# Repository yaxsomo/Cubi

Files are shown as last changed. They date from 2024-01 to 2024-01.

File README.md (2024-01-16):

### Description
Simple open source bluetooth controlled wheeled robot. Mechanical design, electronics and software designs available on this repo.
I used @Gregwar's Holo as a starting point.

The initial design is a cube like robot :

https://www.youtube.com/watch?v=2ZDV0_4vD0g

https://www.youtube.com/watch?v=TOusHRbKWQg

A second design was also made to play around cart-poling:

https://www.youtube.com/watch?v=Ubej95gH9Gs

TODO:

- Add Julien's O. designs and events

- Add Julien's A. and Jérémy's designs and event (cap science)

### Simulation
Some simulation stuff (simple kinematic control, inverted pendulum tests) is available in Python here :
https://bitbucket.org/RemiFabre/cubi/src/master/simulation/

0) Installation
You'll need Python (any version should work) and pygame
```
pip install pygame
```

1) Simple control of a wheeled robot (click around)
```
python main.py
```
https://www.youtube.com/watch?v=O8ZoUAvGYmE

2) Inverted pendulum (cart-pole) simulation
```
python cart_pole.py
```
https://www.youtube.com/watch?v=xhEcLnnj7fg

### How to make it work
You'll have to install the arm cross-compilation tools. On debian-like distributions,
you can get it with:

```
    sudo aptitude install build-essential git-core dfu-util openocd python \
        python-serial binutils-arm-none-eabi gcc-arm-none-eabi libstdc++-arm-none-eabi-newlib
```
If you're running an Ubuntu 14.04 or older, you might need to install the libstdc++-arm-none-eabi-newlib packet by hand. Download link :
http://ftp.de.debian.org/debian/pool/main/libs/libstdc++-arm-none-eabi/libstdc++-arm-none-eabi-newlib_4.8.3-9+4_all.deb

Command (if a conflict rises, you can add --force-overwrite to the following line):
```
	sudo dpkg -i libstdc++-arm-none-eabi-newlib_4.8.3-9+4_all.deb
```

Then go to Cubi/firmware/src and run :

```
bash ./prepare.sh
```

Then, go to the `firmware/` directory and edit the `Makefile` to set the appropriate
`BOARD` variable, targetting your servo.

You can then run:

```
make
```

Use an USB cable to connect your pc with the robot's board

```
make install
```
If you didn't follow this section to setup udev rules, you might need to ```sudo make install``` instead

http://static.leaflabs.com/pub/leaflabs/maple-docs/0.0.12/unix-toolchain.html#toolchain-udev

### Bluetooth
You can control the robot without the need of a cable. The most straight-forward way is to download the "Metabot" app from Google Play. Once on the app you can scan for devices, find your robot and pair it with your phone.

If you want to pair your PC with your robot, one method is as follows (Ubuntu).

Uninstall modemmanager (not needed but causes some issues)

```
    sudo apt-get purge modemmanager
```

Scan for bluetooth devices and save the adress (e.g. 98:D3:37:90:ED:D6) of your robot. For example, we use blueman-manager :

```
    sudo apt-get install blueman
    sudo blueman-manager
```

Assign a serial port to the connection. You can do that on the graphical interface of blueman-manager but doing it directly with rfcomm seems more robust :

```
    sudo rfcomm bind /dev/rfcomm0 98:D3:37:90:ED:D6
```

Now you can access the remote terminal on the robot with :

```
    cu -l /dev/rfcomm0
```

You might have permission access issues. Make sure you're in the dialout group or go bonkers :

```
    sudo chmod 777 /dev/rfcomm0 && cu -l /dev/rfcomm0
```

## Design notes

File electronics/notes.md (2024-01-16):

Pour exporter la board depuis Eagle pour la tirer (Fonctionne sous Eagle 8) :
File->CAM Processor -> Load Job File -> /eagle/sfe-gerb274x.cam  (fichier from Sparkfun)
Gerber RS-274X

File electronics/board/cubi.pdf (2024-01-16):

Pré-placement

On limite les boucles de courant fort. Dans ce cas, ca va être chiant, le connecteur du moteur étant juste complètement débile, la puissance passant sur les broches externe.
On peut quand même remarquer que M1 est gardé par une masse et M2 par VCC. On ajoute donc une capa de découplage entre Vcc et la masse, qui devra être placé au cul du connecteur.

On limite ainsi la casse : en HF, les fils de puissance M1 et M2 sont « blindé » par la masse.

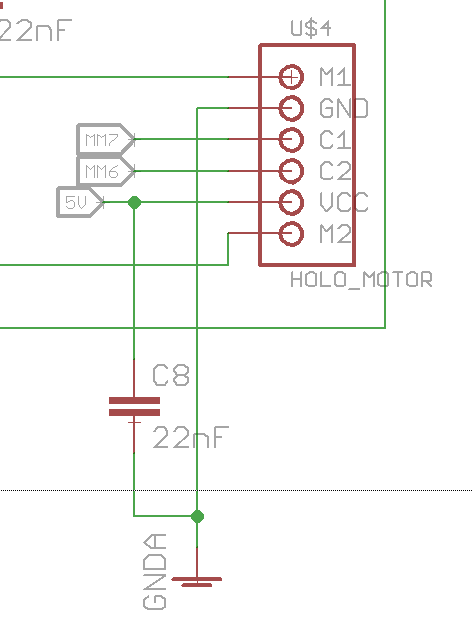
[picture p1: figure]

On place donc les connecteurs au plus court du pont. On limite ainsi les zones dangereuses (en jaune sur la figure). Dans ces zones, on fera particulièrement attention à ne pas fendre le plan de masse. Aucune piste sensible de doit traverser ces zones.

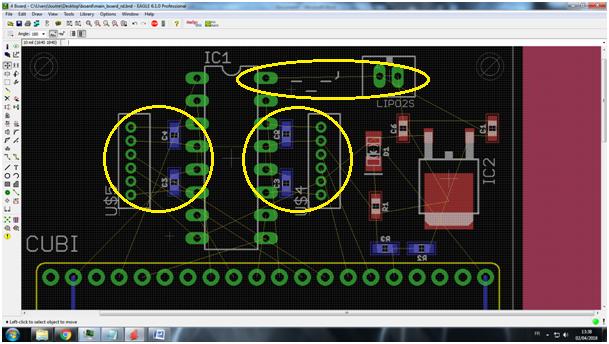
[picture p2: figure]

On tire les pistes fort courant en premier, pour voir à quoi on doit s’attendre. On passe ensuite quelques pistes de commande, pour avoir une idée du routage. On peut essayer de passer une alim au deux.

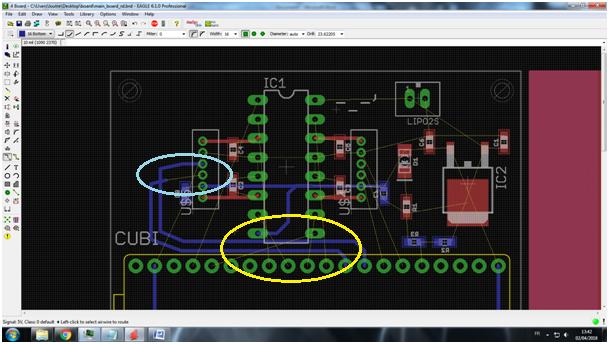
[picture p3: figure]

Premier constat : en bleu, les sorties codeurs croisent. Plus grave en jaune, là on sens que ca va être Beyrouth. Après étude du schéma, on voie que les fils non routé sont les PWM, donc des signaux rapide. Tant pis pour l’alim, elle dégage, on privilégie les signaux rapide au routage. On en profite pour réafecter les E/S pour que cela ne croise pas.

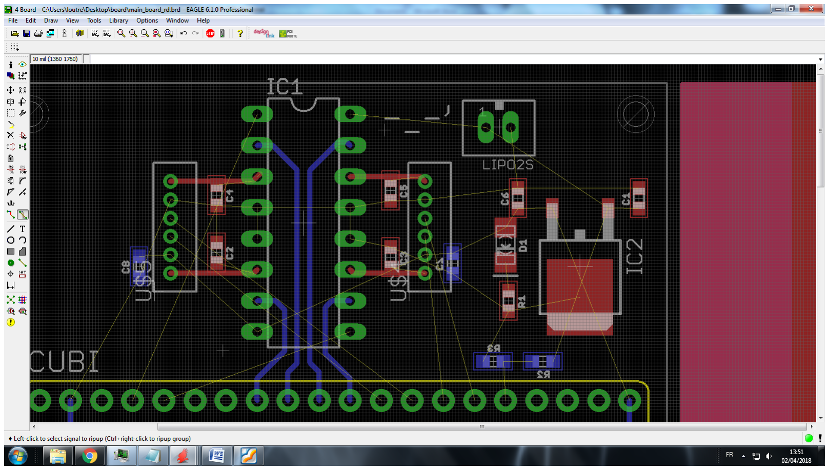
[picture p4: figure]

On passe toutes les PWM en BOTTOM : comme cela, le plan de masse en top fera écran (passer des pistes sous un composant de puissance, c’est dangereux, le composant rayonne, ce qui peut pourris les signaux)

On reprend le routage des codeurs :

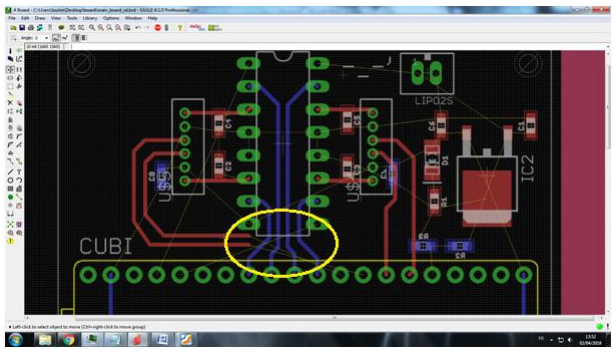
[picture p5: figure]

En jaune, c’est la seconde guerre du Golf. On doit croiser les codeurs avec les PWM, donc fendre le plan de masse. Or, pour rappel, règle N°1 en routage : ON NE FEND JAMAIS UN PLAN DE MASSE (Bordel). Bon, là on est en deux couches donc, on se détend.
Règle N°2 du routage : en deux couches, si on doit croiser des pistes, on se réfère à la règle N°1.

Dans notre cas, on fait le tour par le haut.

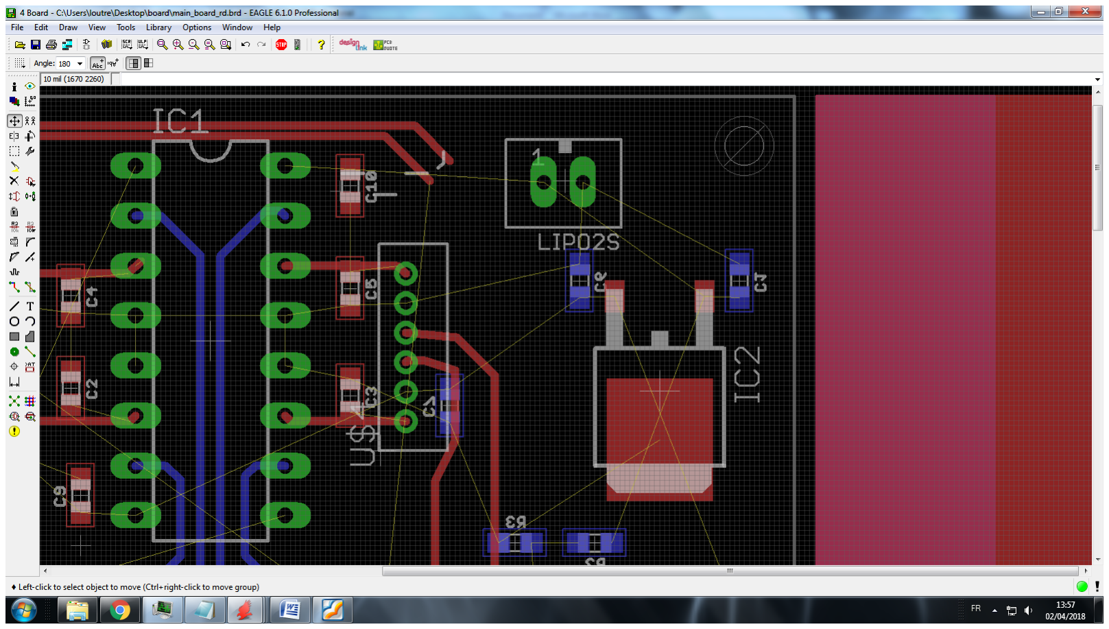
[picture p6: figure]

Bon c’est pas top. Mais a défaut… on va croiser l’alim mais avec les capas de découplages ca devrait aller (Les capas sur VCC1 et VCC2 ont été ajouté, elles avaient été oublié)

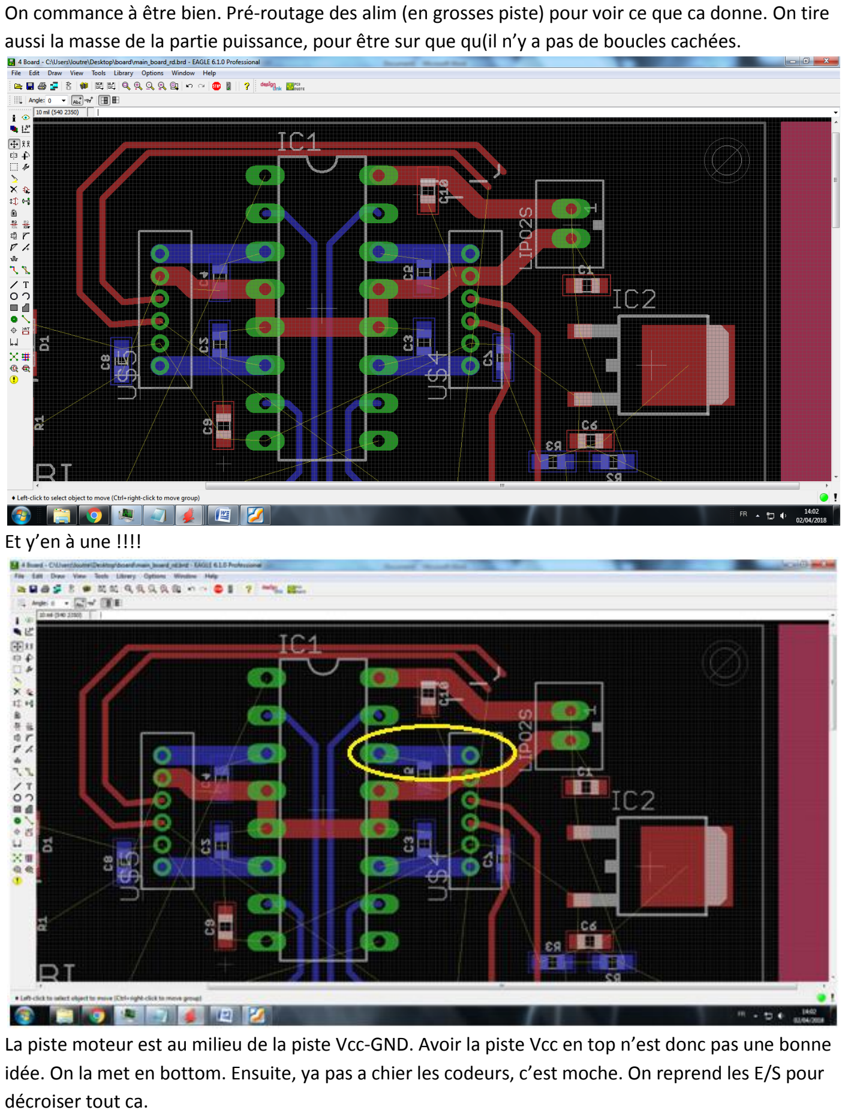
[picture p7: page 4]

On commance à être bien. Pré-routage des alim (en grosses piste) pour voir ce que ca donne. On tire aussi la masse de la partie puissance, pour être sur que qu(il n’y a pas de boucles cachées.

Et y’en à une !!!!

La piste moteur est au milieu de la piste Vcc-GND. Avoir la piste Vcc en top n’est donc pas une bonne idée. On la met en bottom. Ensuite, ya pas a chier les codeurs, c’est moche. On reprend les E/S pour décroiser tout ca.

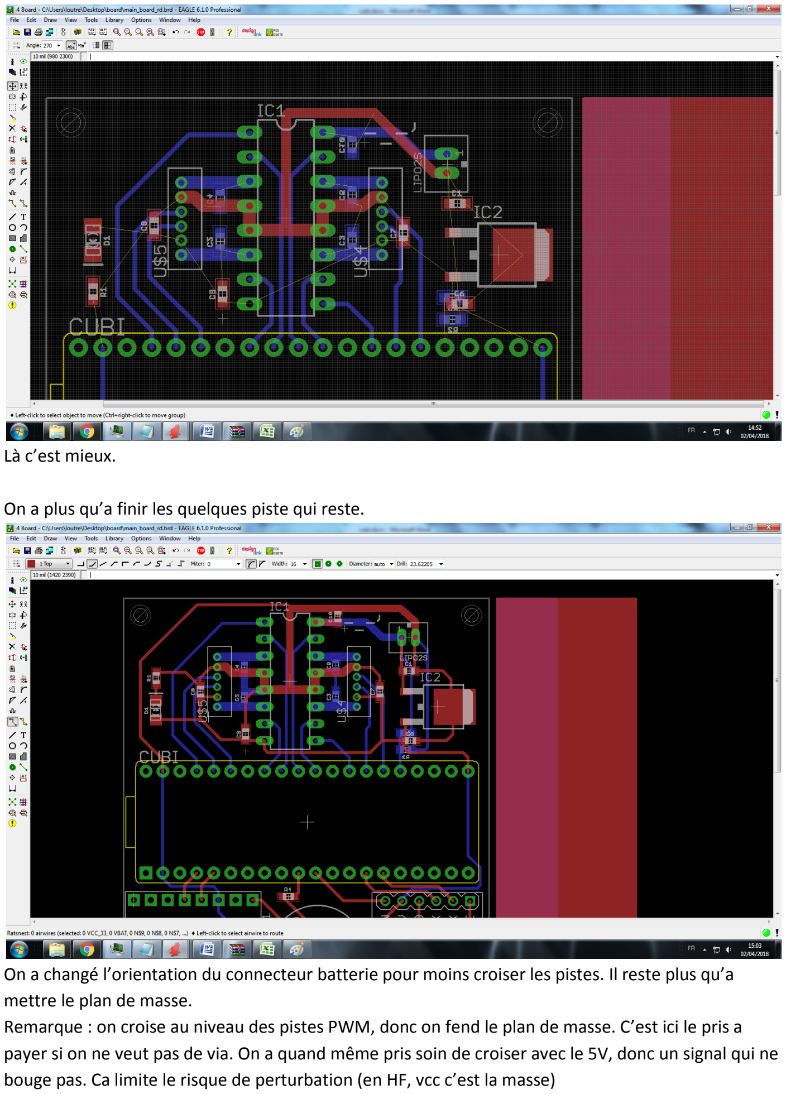
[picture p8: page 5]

Là c’est mieux.

On a plus qu’a finir les quelques piste qui reste.

On a changé l’orientation du connecteur batterie pour moins croiser les pistes. Il reste plus qu’a mettre le plan de masse.
Remarque : on croise au niveau des pistes PWM, donc on fend le plan de masse. C’est ici le pris a payer si on ne veut pas de via. On a quand même pris soin de croiser avec le 5V, donc un signal qui ne bouge pas. Ca limite le risque de perturbation (en HF, vcc c’est la masse)

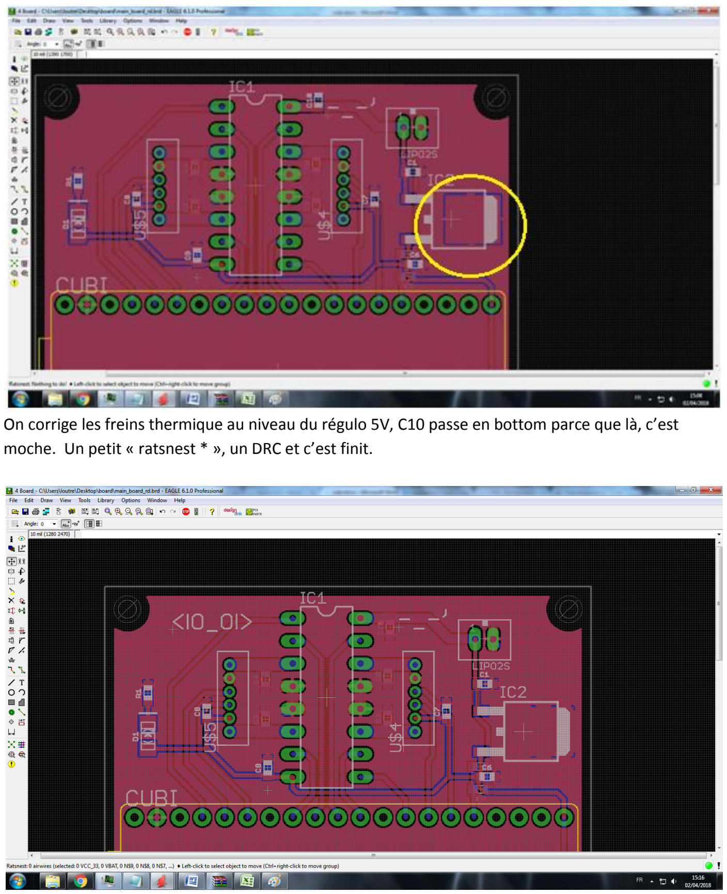
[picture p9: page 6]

On corrige les freins thermique au niveau du régulo 5V, C10 passe en bottom parce que là, c’est moche. Un petit « ratsnest * », un DRC et c’est finit.

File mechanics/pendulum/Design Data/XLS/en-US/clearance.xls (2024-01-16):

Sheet: Ansi Unified Screw Threads
I | Sort Order -1
Fastener Type | Size | Shaft Diameters |  |  | Head Dimensions
 |  | Close | Normal | Loose | Diameter | Depth/Angle | Head Type
Flat Head Machine Screw (82) | #0 | 0.0635 | 0.07 | 0.073 | 0.119 | 82 | 2
Flat Head Machine Screw (82) | #1 | 0.076 | 0.081 | 0.089 | 0.146 | 82 | 2
Flat Head Machine Screw (82) | #2 | 0.089 | 0.096 | 0.1065 | 0.172 | 82 | 2
Flat Head Machine Screw (82) | #3 | 0.104 | 0.11 | 0.12 | 0.199 | 82 | 2
Flat Head Machine Screw (82) | #4 | 0.116 | 0.1285 | 0.136 | 0.225 | 82 | 2
Flat Head Machine Screw (82) | #5 | 0.1285 | 0.136 | 0.154 | 0.252 | 82 | 2
Flat Head Machine Screw (82) | #6 | 0.144 | 0.1495 | 0.1695 | 0.279 | 82 | 2
Flat Head Machine Screw (82) | #8 | 0.1695 | 0.177 | 0.1935 | 0.332 | 82 | 2
Flat Head Machine Screw (82) | #10 | 0.196 | 0.201 | 0.221 | 0.385 | 82 | 2
Flat Head Machine Screw (82) | #12 | 0.221 | 0.228 | 0.246 | 0.438 | 82 | 2
Flat Head Machine Screw (82) | 1/4 | 0.257 | 0.266 | 0.2812 | 0.507 | 82 | 2
Flat Head Machine Screw (82) | 5/16 | 0.323 | 0.332 | 0.3437 | 0.635 | 82 | 2
Flat Head Machine Screw (82) | 3/8 | 0.386 | 0.397 | 0.4062 | 0.762 | 82 | 2
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

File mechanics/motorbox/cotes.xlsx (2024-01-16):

epaisseur | 5 | mm | épaisseur du bois
ecartement | 20 | mm | ecartement entre les deux moteurs
dvis | 3 | mm | diametre vis
largeur | 32 | mm | largeur de la boite moteur
L_fente | 30 | mm | longeur des fentes latéral
L_attache_carte | 15 | mm | longueur du bord pour fixer la plaque de la carte elec
marge_attache_carte | 5 | mm | marge entre la plaque carte et la plaque moteur

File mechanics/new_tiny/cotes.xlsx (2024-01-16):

epaisseur | 6 | mm | épaisseur du bois
ecartement | 25 | mm | ecartement entre les deux moteurs
dvis | 3 | mm | diametre vis
largeur | 32 | mm | largeur de la boite moteur
L_fente | 30 | mm | longeur des fentes latéral
L_attache_carte | 15 | mm | longueur du bord pour fixer la plaque de la carte elec
marge_attache_carte | 5 | mm | marge entre la plaque carte et la plaque moteur
L_cubi | 81.6 | mm | longeur de la boite cubi
largeur_cubi | 81.6 | mm | largeur du cubi
L_moteur | 28.3 | mm | Longeur moteur sans l'axe
marge_trou | 2 | mm | marge entre les trous et le bord
taille_trou | 7 | mm
H_cubi | 81.6 | mm | hauteur cubi
d_wheel | 60 | mm | diametre wheel
epaisseur_wheel | 9 | mm
H_nez | 25 | mm
H_trou_nez | 10 | mm
chanfrein | 0.5 | mm
H_trou_int | 0.2 | mm | hauteur des aspérités à l'intérieur des troues
L_trou_int | 1 | mm
pos_trou_int_1 | 0.7 | mm | position aspérités intérieur 1
pos_trou_int_2 | 3 | mm | position aspérités intérieur 2
epaisseur_modules | 6 | mm
L_modules | 20 | mm | longueur pour mettre les modules complémentaires
L_metabois | 8.2 | mm
epaisseur_metabois | 3 | mm

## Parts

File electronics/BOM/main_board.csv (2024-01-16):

Part | Value | Device | Package | Description | MF | MPN | OC_FARNELL | OC_NEWARK | PROD_ID | VALUE | Link | bundle_number | bundle_price | Unit price
C1 | 0.1uF | 0.1UF-0603-25V-(+80/-20%) | 603 | 0.1µF ceramic capacitors |  |  |  |  | CAP-00810 | 0.1uF | https://fr.aliexpress.com/item/Durable-in-Use-0603-SMD-Chip-Capacitors-0-5pF-2-2uF-90Valuesx50-Sample-Book-Assortment-Kit/32721099737.html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 |  |  | 0.01
C2 | 22nF | 22NF/22,000PF-0603-50V-10% | 603 | 0.022uF/22nF/22,000pF ceramic capacitors |  |  |  |  | CAP-07885 | 22nF |  |  |  | 0.01
C3 | 22nF | 22NF/22,000PF-0603-50V-10% | 603 | 0.022uF/22nF/22,000pF ceramic capacitors |  |  |  |  | CAP-07885 | 22nF |  |  |  | 0.01
C4 | 22nF | 22NF/22,000PF-0603-50V-10% | 603 | 0.022uF/22nF/22,000pF ceramic capacitors |  |  |  |  | CAP-07885 | 22nF |  |  |  | 0.01
C5 | 22nF | 22NF/22,000PF-0603-50V-10% | 603 | 0.022uF/22nF/22,000pF ceramic capacitors |  |  |  |  | CAP-07885 | 22nF |  |  |  | 0.01
C6 | 0.1uF | 0.1UF-0603-25V-(+80/-20%) | 603 | 0.1µF ceramic capacitors |  |  |  |  | CAP-00810 | 0.1uF |  |  |  | 0.01
D1 |  | LED-FKIT-1206 | FKIT-LED-1206 | LED (Generic) |  |  |  |  |  |  | https://fr.aliexpress.com/item/1206-SMD-LED-SMD-LED-blue-green-and-white-bag-sample-pack-5-colors-each-20/32289160842.html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 |  |  | 0.01
D2 |  | LED-FKIT-1206 | FKIT-LED-1206 | LED (Generic) |  |  |  |  |  |  |  |  |  | 0.01
IC1 | L293D | L293D | DIL16 | PUSH-PULL 4 CHANNEL DRIVER |  | L293D | 9589619 | 56P8249 |  |  | https://fr.aliexpress.com/item/50-PCS-L293D-DIP16-L293-DIP-nouveau-original-livraison-gratuite/32861102517.html | 50 | 11.01 | 0.2202
IC2 | MC78M05ABDT | MC78M05ABDT | DPACK_3 | 500 mA Positive Voltage Regulators |  |  |  |  |  |  | https://fr.aliexpress.com/item/Free-shipping-20pcs-New-78M05-TO252-7805-750mA/32617637330.html | 30 | 1.03 | 0.0343333333
LIPO2S | JST-PH_2-PIN_HEADER | JST-PH_2-PIN_HEADER | JST_B2B-PH_HEADER | 2-pin JST PH Shrouded Header, top entry
R1 | 133 | 0.27OHM-0603-1/10W-1% | 603 | resistor |  |  |  |  | RES-08787 | 0.27 | https://fr.aliexpress.com/item/0603-SMD-Resistor-Kit-Assorted-Kit-1-chip-resistor-element-170-values-50pcs/32546720452.html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
R2 | 60k | 0.27OHM-0603-1/10W-1% | 603 | resistor |  |  |  |  | RES-08787 | 0.27 |  |  |  | 0.01
R3 | 30k | 0.27OHM-0603-1/10W-1% | 603 | resistor |  |  |  |  | RES-08787 | 0.27 |  |  |  | 0.01
R4 | 100 | 0.27OHM-0603-1/10W-1% | 603 | resistor |  |  |  |  | RES-08787 | 0.27 |  |  |  | 0.01
R5 | 133 | 0.27OHM-0603-1/10W-1% | 603 | resistor |  |  |  |  | RES-08787 | 0.27 |  |  |  | 0.01
SG1 | F/CM12P | F/CM12P | F/CM12P | BUZZER Source: Buerklin |  |  | unknown | unknown |  |  | https://fr.aliexpress.com/item/5PCS-Lot-Passive-Buzzer-AC-12MM-8-5MM-12085-16R-Resistance-3V-5V-9V-12V-In/32503620431.html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 | 10 | 0.95 | 0.095
U$1 | MAPLEMINI | MAPLEMINI | 20-DIP |  |  |  |  |  |  |  | https://fr.aliexpress.com/item/5PCS-LOT-leaflabs-Leaf-maple-mini-ARM-STM32-compatibility/1400682373.html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 | 5 | 14.43 | 2.886
U$3 | WIRELESS-BLUETOOTH-HC-05 | WIRELESS-BLUETOOTH-HC-05 | WIRELESS-BLUETOOTH-HC-05 | Bluetooth Transceiver Module based on HC-05 board |  |  |  |  |  |  | https://fr.aliexpress.com/item/HC05-HC-05-master-slave-6pin-JY-MCU-anti-reverse-integrated-Bluetooth-serial-pass-through-module/32272705461.html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 | 5 | 13 | 2.6
U$4 | HOLO_MOTOR | HOLO_MOTOR | HOLO_MOTOR |  |  |  |  |  |  |  | https://fr.aliexpress.com/item/5PCS-Well-made-GA12-N20-dc-gear-motor-with-encoder-speed-velocity-measurement-6V-500rpm-FOR/32615345501.html | 5 | 39.3 | 7.86
U$5 | HOLO_MOTOR | HOLO_MOTOR | HOLO_MOTOR |  |  |  |  |  |  |  |  |  |  | 7.86
U$6 | GY-85 | GY-85 | GY-85 |  |  |  |  |  |  |  | https://fr.aliexpress.com/item/GY-85-BMP085-Sensor-Modules-9-Axis-Sensor-Module-ITG3205-ADXL345-HMC5883L-6DOF-9DOF-IMU-Sensor/2024503421.html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 | 1 | 8.17 | 8.17
 |  | 9V Battery Snap connector |  |  |  |  |  |  |  |  | https://fr.aliexpress.com/item/10pcs-9V-Battery-Snap-Connector-clip-Lead-Wires-holder/32825539506.html | 10 | 0.82 | 0.082
 |  | 9V rechargeable Battery |  |  |  |  |  |  |  |  | https://fr.aliexpress.com/item/1pcs-ZNTER-9V-400mAh-lithium-li-po-li-ion-rechargeable-battery-micro-usb-cable-for-charging/32805810958.html | 2 | 14.14 | 7.07
 |  |  |  |  |  |  |  |  |  |  |  |  | Total | 36.9975333333

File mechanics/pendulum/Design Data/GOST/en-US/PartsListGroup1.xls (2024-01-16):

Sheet: Лист 1
Инв. № подл |  |  |  | Подп. и дата | Взам. инв. № | Инв. № дубл. |  |  | Подп. и дата
Формат | Зона | Поз. | Обозначение |  |  |  | Наименование |  |  |  |  |  | Кол. на исполнение
 |  |  |  |  |  |  |  |  |  |  |  | Лит.
 |  |  |  |  |  |  |  |  |  |  |  | Код
 |  |  |  |  |  |  |  | Изм. | Лист | № докум | Подпись |  | Дата
 |  |  |  |  |  |  |  | Разраб.
 |  |  |  |  |  |  |  | Пров.
 |  |  |  |  |  |  |  | Н.контр
 |  |  |  |  |  |  |  | Утв.
 |  |  |  |  |  |  |  |  |  |  |  |  |  | Копировал

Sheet: Лист 2
Инв. № подл |  |  |  | Подп. и дата | Взам. инв. № | Инв. № дубл. |  |  | Подп. и дата
Формат | Зона | Поз. | Обозначение |  |  |  | Наименование |  |  |  |  | Кол. на исполнение
 |  |  |  |  |  |  |  | Изм. | Лист | № докум. | Подп. | Дата
 |  |  |  |  |  |  |  |  |  |  |  |  | Копировал
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

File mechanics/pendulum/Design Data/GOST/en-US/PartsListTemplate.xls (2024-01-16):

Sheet: Лист 1
 | Формат | Зона |  | Поз. |  | Обозначение |  |  |  | Наименование |  |  |  | Кол. | Приме-чание
Подп. и дата
Инв. № дубл.
Взам. инв. №
Подп. и дата
 | Изм. |  | Лист |  | № докум |  | Подпись | Дата
Инв. № подл | Разраб. |  |  |  |  |  |  |  |  |  | Литера |  | Лист |  |  | Листов
 | Пров.
 | Н.контр
 | Утв.
 |  |  |  |  |  |  |  |  | Копировал |  |  | Формат А4

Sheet: Лист 2
 | Формат | Зона |  | Поз. |  | Обозначение |  |  |  | Наименование |  | Кол. | Приме-чание
Подп. и дата
Инв. № дубл.
Взам. инв. №
Подп. и дата
Инв. № подл
 | Изм. |  | Лист |  | № докум. |  | Подп. |  | Дата
 |  |  |  |  |  |  |  | Копировал |  |  | Формат А4
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

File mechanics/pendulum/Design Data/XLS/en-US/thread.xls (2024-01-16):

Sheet: Inch Tapping Threads
I Q X | Inch Tapping Threads |  | Sort Order - 5 |  | External |  |  |  |  |  |  | Internal
 |  |  |  |  |  | Major Dia |  | Pitch Dia |  | Minor Dia |  |  | Minor Dia |  | Pitch Dia |  | Major Dia |  | Tap Drill
Size | Size Suffix | Thread Designation | Custom Thread Designation | TPI | Class | Max | Min | Max | Min | Max | Min | Class | Min | Max | Min | Max | Min | Max | Basic
0.0600 |  | 0-48 | 0-48 | 48 | 2B | 0.0600 | 0.0540 | 0.0480 | 0.0435 | 0.0360 | 0.0330
0.0730 |  | 1-42 | 1-42 | 42 | 2B | 0.0750 | 0.0690 | 0.0620 | 0.0575 | 0.0490 | 0.0460
0.0860 |  | 2-32 | 2-32 | 32 | 2B | 0.0880 | 0.0820 | 0.0760 | 0.0710 | 0.0640 | 0.0600
0.0990 |  | 3-28 | 3-28 | 28 | 2B | 0.1010 | 0.0950 | 0.0880 | 0.0830 | 0.0750 | 0.0710
0.1120 |  | 4-24 | 4-24 | 24 | 2B | 0.1140 | 0.1080 | 0.1000 | 0.0950 | 0.0860 | 0.0820
0.1250 |  | 5-20 | 5-20 | 20 | 2B | 0.1300 | 0.1230 | 0.1120 | 0.1065 | 0.0940 | 0.0900
0.1380 |  | 6-20 | 6-20 | 20 | 2B | 0.1390 | 0.1320 | 0.1215 | 0.1155 | 0.1040 | 0.0990
0.1510 |  | 7-19 | 7-19 | 19 | 2B | 0.1540 | 0.1470 | 0.1345 | 0.1280 | 0.1150 | 0.1090
0.1640 |  | 8-18 | 8-18 | 18 | 2B | 0.1660 | 0.1590 | 0.1440 | 0.1375 | 0.1220 | 0.1160
0.1900 |  | 10-16 | 10-16 | 16 | 2B | 0.1890 | 0.1820 | 0.1650 | 0.1585 | 0.1410 | 0.1350
0.2160 |  | 12-14 | 12-14 | 14 | 2B | 0.2150 | 0.2080 | 0.1895 | 0.1825 | 0.1640 | 0.1570
0.2420 |  | 14-14 | 14-14 | 14 | 2B | 0.2410 | 0.2340 | 0.2130 | 0.2060 | 0.1850 | 0.1780
0.2500 |  | 1/4-14 | 1/4-14 | 14 | 2B | 0.2460 | 0.2370 | 0.2190 | 0.2110 | 0.1920 | 0.1850
0.3125 |  | 5/16-12 | 5/16-12 | 12 | 2B | 0.3150 | 0.3060 | 0.2795 | 0.2710 | 0.2440 | 0.2360
0.3750 |  | 3/8-12 | 3/8-12 | 12 | 2B | 0.3800 | 0.3710 | 0.3445 | 0.3350 | 0.3090 | 0.2990
0.4375 |  | 7/16-10 | 7/16-10 | 10 | 2B | 0.4400 | 0.4290 | 0.3995 | 0.3890 | 0.3590 | 0.3490
0.5000 |  | 1/2-10 | 1/2-10 | 10 | 2B | 0.5040 | 0.4930 | 0.4635 | 0.4530 | 0.4230 | 0.4130

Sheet: Metric Forming Screw Threads
M P X | Metric Forming Screw Threads |  | Sort Order - 6 |  | External |  |  |  |  |  |  | Internal
 |  |  |  |  |  | Major Dia |  | Pitch Dia |  | Minor Dia |  |  | Minor Dia |  | Pitch Dia |  | Major Dia |  | Tap Drill
Size | Size Suffix | Thread Designation | Custom Thread Designation | Pitch | Class | Max | Min | Max | Min | Max | Min | Class | Min | Max | Min | Max | Min | Max | Basic
1.5 |  | 1.5x0.5 | 1.5x0.5 | 0.5 | 6g | 1.520 | 1.380 | 1.215 | 1.110 | 0.910 | 0.840
1.5 |  | ST1.5x0.5 | ST1.5x0.5 | 0.5 | 6g | 1.520 | 1.380 | 1.215 | 1.110 | 0.910 | 0.840
1.9 |  | 1.9x0.6 | 1.9x0.6 | 0.6 | 6g | 1.900 | 1.760 | 1.570 | 1.465 | 1.240 | 1.170
1.9 |  | ST1.9x0.6 | ST1.9x0.6 | 0.6 | 6g | 1.900 | 1.760 | 1.570 | 1.465 | 1.240 | 1.170
2.2 |  | 2.2x0.8 | 2.2x0.8 | 0.8 | 6g | 2.240 | 2.100 | 1.935 | 1.810 | 1.630 | 1.520
2.2 |  | ST2.2x0.8 | ST2.2x0.8 | 0.8 | 6g | 2.240 | 2.100 | 1.935 | 1.810 | 1.630 | 1.520
2.6 |  | 2.6x0.9 | 2.6x0.9 | 0.9 | 6g | 2.570 | 2.430 | 2.235 | 2.115 | 1.900 | 1.800
2.6 |  | ST2.6x0.9 | ST2.6x0.9 | 0.9 | 6g | 2.570 | 2.430 | 2.235 | 2.115 | 1.900 | 1.800
2.9 |  | 2.9x1 | 2.9x1 | 1 | 6g | 2.900 | 2.760 | 2.540 | 2.420 | 2.180 | 2.080
2.9 |  | 2.9x1.1 | 2.9x1.1 | 1.1 | 6g | 2.900 | 2.760 | 2.540 | 2.420 | 2.180 | 2.080
2.9 |  | ST2.9x1.1 | ST2.9x1.1 | 1.1 | 6g | 2.900 | 2.760 | 2.540 | 2.420 | 2.180 | 2.080
2.9 |  | 2.9x1.3 | 2.9x1.3 | 1.3 | 6g | 2.900 | 2.720 | 2.540 | 2.355 | 1.890 | 1.700
2.9 |  | 2.9x1.4 | 2.9x1.4 | 1.4 | 6g | 2.900 | 2.720 | 2.340 | 2.175 | 1.780 | 1.630
3.3 |  | 3.3x1.3 | 3.3x1.3 | 1.3 | 6g | 3.300 | 3.120 | 2.795 | 2.665 | 2.290 | 2.210
3.3 |  | ST3.3x1.3 | ST3.3x1.3 | 1.3 | 6g | 3.300 | 3.120 | 2.795 | 2.665 | 2.290 | 2.210
3.5 |  | 3.5x1.3 | 3.5x1.3 | 1.3 | 6g | 3.530 | 3.350 | 3.085 | 2.930 | 2.640 | 2.510
3.5 |  | ST3.5x1.3 | ST3.5x1.3 | 1.3 | 6g | 3.530 | 3.350 | 3.085 | 2.930 | 2.640 | 2.510
3.5 |  | 3.5x1.6 | 3.5x1.6 | 1.6 | 6g | 3.530 | 3.350 | 2.920 | 2.755 | 2.310 | 2.160
3.5 |  | 3.5x3.2 | 3.5x3.2 | 3.2 | 6g | 3.530 | 3.310 | 2.800 | 2.600 | 2.070 | 1.890
3.9 |  | 3.9x1.3 | 3.9x1.3 | 1.3 | 6g | 3.910 | 3.730 | 3.415 | 3.250 | 2.920 | 2.770
3.9 |  | ST3.9x1.3 | ST3.9x1.3 | 1.3 | 6g | 3.910 | 3.730 | 3.415 | 3.250 | 2.920 | 2.770
3.9 |  | 3.9x1.6 | 3.9x1.6 | 1.6 | 6g | 3.910 | 3.730 | 3.300 | 3.135 | 2.690 | 2.540
3.9 |  | 3.9x3.2 | 3.9x3.2 | 3.2 | 6g | 3.910 | 3.690 | 3.180 | 2.980 | 2.450 | 2.270
4.2 |  | 4.2x1.4 | 4.2x1.4 | 1.4 | 6g | 4.220 | 4.040 | 3.660 | 3.495 | 3.100 | 2.950
4.2 |  | ST4.2x1.4 | ST4.2x1.4 | 1.4 | 6g | 4.220 | 4.040 | 3.660 | 3.495 | 3.100 | 2.950
4.2 |  | 4.2x1.6 | 4.2x1.6 | 1.6 | 6g | 4.220 | 4.040 | 3.610 | 3.445 | 3.000 | 2.850
4.2 |  | 4.2x3.2 | 4.2x3.2 | 3.2 | 6g | 4.220 | 4.000 | 3.380 | 3.180 | 2.540 | 2.360
4.8 |  | 4.8x1.6 | 4.8x1.6 | 1.6 | 6g | 4.800 | 4.620 | 4.190 | 4.025 | 3.580 | 3.430
4.8 |  | ST4.8x1.6 | ST4.8x1.6 | 1.6 | 6g | 4.800 | 4.620 | 4.190 | 4.025 | 3.580 | 3.430
4.8 |  | 4.8x1.8 | 4.8x1.8 | 1.8 | 6g | 4.800 | 4.620 | 4.065 | 3.885 | 3.330 | 3.150
4.8 |  | 4.8x3.2 | 4.8x3.2 | 3.2 | 6g | 4.800 | 4.580 | 3.960 | 3.760 | 3.120 | 2.940
5.5 |  | 5.5x1.8 | 5.5x1.8 | 1.8 | 6g | 5.460 | 5.280 | 4.815 | 4.635 | 4.170 | 3.990
5.5 |  | ST5.5x1.8 | ST5.5x1.8 | 1.8 | 6g | 5.460 | 5.280 | 4.815 | 4.635 | 4.170 | 3.990
6.3 |  | 6.3x1.8 | 6.3x1.8 | 1.8 | 6g | 6.250 | 6.030 | 5.565 | 5.365 | 4.880 | 4.700
6.3 |  | ST6.3x1.8 | ST6.3x1.8 | 1.8 | 6g | 6.250 | 6.030 | 5.565 | 5.365 | 4.880 | 4.700
8.0 |  | 8x2.1 | 8x2.1 | 2.1 | 6g | 8.000 | 7.780 | 7.100 | 6.885 | 6.200 | 5.990
8.0 |  | ST8x2.1 | ST8x2.1 | 2.1 | 6g | 8.000 | 7.780 | 7.100 | 6.885 | 6.200 | 5.990
9.5 |  | 9.5x2.1 | 9.5x2.1 | 2.1 | 6g | 9.650 | 9.430 | 8.750 | 8.510 | 7.850 | 7.590
9.5 |  | ST9.5x2.1 | ST9.5x2.1 | 2.1 | 6g | 9.650 | 9.430 | 8.750 | 8.510 | 7.850 | 7.590

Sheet: ISO Pipe Threads
M Q | ISO Pipe Threads |  | Sort Order - 9 |  | External |  |  |  |  |  |  | Internal
 |  |  |  |  |  | Major Dia |  | Pitch Dia |  | Minor Dia |  |  | Minor Dia |  | Pitch Dia |  | Major Dia |  | Tap Drill | Thread Depth | Thread Runouts
Size | Size Suffix | Thread Designation | Custom Thread Designation | TPI | Class | Max | Min | Max | Min | Max | Min | Class | Min | Max | Min | Max | Min | Max | Basic
7.723 |  | G7.723x0.907 | G 1/16 | 28 | A | 7.723 | 7.509 | 7.142 | 7.035 | 6.561 |  |  | 6.561 | 6.834 | 7.142 | 7.249 | 7.723 |  | 1.5875 | 15.446 | 4.5000
7.723 |  | G7.723x0.907 | G 1/16 | 28 | B | 7.723 | 7.509 | 7.142 | 6.928 | 6.561
9.728 |  | G9.728x0.907 | G 1/8 | 28 | A | 9.728 | 9.514 | 9.147 | 9.040 | 8.566 |  |  | 8.566 | 8.848 | 9.147 | 9.254 | 9.728 |  | 3.1750 | 19.456 | 4.5000
9.728 |  | G9.728x0.907 | G 1/8 | 28 | B | 9.728 | 9.514 | 9.147 | 8.933 | 8.566
13.157 |  | G13.157x1.337 | G 1/4 | 19 | A | 13.157 | 12.907 | 12.301 | 12.176 | 11.445 |  |  | 11.445 | 11.89 | 12.301 | 12.426 | 13.157 |  | 6.3500 | 26.314 | 6.5000
13.157 |  | G13.157x1.337 | G 1/4 | 19 | B | 13.157 | 12.907 | 12.301 | 12.051 | 11.445
16.662 |  | G16.662x1.337 | G 3/8 | 19 | A | 16.662 | 16.412 | 15.806 | 15.681 | 14.950 |  |  | 14.95 | 15.395 | 15.806 | 15.931 | 16.662 |  | 9.5250 | 33.324 | 6.5000
16.662 |  | G16.662x1.337 | G 3/8 | 19 | B | 16.662 | 16.412 | 15.806 | 15.556 | 14.950
20.955 |  | G20.955x1.814 | G 1/2 | 14 | A | 20.955 | 20.671 | 19.793 | 19.651 | 18.631 |  |  | 18.631 | 19.172 | 19.793 | 19.935 | 20.955 |  | 12.7000 | 41.910 | 8.5000
20.955 |  | G20.955x1.814 | G 1/2 | 14 | B | 20.955 | 20.671 | 19.793 | 19.509 | 18.631
22.911 |  | G22.911x1.814 | G 5/8 | 14 | A | 22.911 | 22.627 | 21.749 | 21.607 | 20.587 |  |  | 20.587 | 21.128 | 21.749 | 21.891 | 22.911 |  |  | 45.822 | 8.5000
22.911 |  | G22.911x1.814 | G 5/8 | 14 | B | 22.911 | 22.627 | 21.749 | 21.465 | 20.587
26.441 |  | G26.441x1.814 | G 3/4 | 14 | A | 26.441 | 26.157 | 25.279 | 25.137 | 24.117 |  |  | 24.117 | 24.658 | 25.279 | 25.421 | 26.441 |  | 15.8750 | 52.882 | 8.5000
26.441 |  | G26.441x1.814 | G 3/4 | 14 | B | 26.441 | 26.157 | 25.279 | 24.995 | 24.117
30.201 |  | G30.201x1.814 | G 7/8 | 14 | A | 30.201 | 29.917 | 29.039 | 28.897 | 27.877 |  |  | 27.877 | 28.418 | 29.039 | 29.181 | 30.201 |  | 22.2250 | 60.402 | 8.5000
30.201 |  | G30.201x1.814 | G 7/8 | 14 | B | 30.201 | 29.917 | 29.039 | 28.755 | 27.877
33.249 |  | G33.249x2.309 | G 1 | 11 | A | 33.249 | 32.889 | 31.770 | 31.590 | 30.291 |  |  | 30.291 | 30.931 | 31.77 | 31.95 | 33.249 |  | 25.4000 | 66.498 | 10.0000
33.249 |  | G33.249x2.309 | G 1 | 11 | B | 33.249 | 32.889 | 31.770 | 31.410 | 30.291
37.897 |  | G37.897x2.309 | G 1 1/8 | 11 | A | 37.897 | 37.537 | 36.418 | 36.238 | 34.939 |  |  | 34.939 | 35.579 | 36.418 | 36.598 | 37.897 |  | 28.5750 | 75.794 | 10.0000
37.897 |  | G37.897x2.309 | G 1 1/8 | 11 | B | 37.897 | 37.537 | 36.418 | 36.058 | 34.939
41.910 |  | G41.91x2.309 | G 1 1/4 | 11 | A | 41.910 | 41.550 | 40.431 | 40.251 | 38.952 |  |  | 38.952 | 39.592 | 40.431 | 40.611 | 41.910 |  | 31.7500 | 83.820 | 10.0000
41.910 |  | G41.91x2.309 | G 1 1/4 | 11 | B | 41.910 | 41.550 | 40.431 | 40.071 | 38.952
47.803 |  | G47.803x2.309 | G 1 1/2 | 11 | A | 47.803 | 47.443 | 46.324 | 46.144 | 44.845 |  |  | 44.845 | 45.485 | 46.324 | 46.504 | 47.803 |  | 38.1000 | 95.606 | 10.0000
47.803 |  | G47.803x2.309 | G 1 1/2 | 11 | B | 47.803 | 47.443 | 46.324 | 45.964 | 44.845
53.746 |  | G53.746x2.309 | G 1 3/4 | 11 | A | 53.746 | 53.386 | 52.267 | 52.087 | 50.788 |  |  | 50.788 | 51.428 | 52.267 | 52.447 | 53.746 |  | 44.4500 | 107.492 | 10.0000
53.746 |  | G53.746x2.309 | G 1 3/4 | 11 | B | 53.746 | 53.386 | 52.267 | 51.907 | 50.788
59.614 |  | G59.614x2.309 | G 2 | 11 | A | 59.614 | 59.254 | 58.135 | 57.955 | 56.656 |  |  | 56.656 | 57.296 | 58.135 | 58.315 | 59.614 |  | 50.8000 | 119.228 | 10.0000
59.614 |  | G59.614x2.309 | G 2 | 11 | B | 59.614 | 59.254 | 58.135 | 57.775 | 56.656
65.710 |  | G65.71x2.309 | G 2 1/4 | 11 | A | 65.710 | 65.276 | 64.231 | 64.014 | 62.752 |  |  | 62.752 | 63.392 | 64.231 | 64.448 | 65.710 |  | 57.1500 | 131.420 | 10.0000
65.710 |  | G65.71x2.309 | G 2 1/4 | 11 | B | 65.710 | 65.276 | 64.231 | 63.797 | 62.752
75.184 |  | G75.184x2.309 | G 2 1/2 | 11 | A | 75.184 | 74.750 | 73.705 | 73.488 | 72.226 |  |  | 72.226 | 72.866 | 73.705 | 73.922 | 75.184 |  |  | 150.368 | 10.0000
75.184 |  | G75.184x2.309 | G 2 1/2 | 11 | B | 75.184 | 74.750 | 73.705 | 73.271 | 72.226
81.534 |  | G81.534x2.309 | G 2 3/4 | 11 | A | 81.534 | 81.100 | 80.055 | 79.838 | 78.576 |  |  | 78.576 | 79.216 | 80.055 | 80.272 | 81.534 |  | 69.8500 | 163.068 | 10.0000
81.534 |  | G81.534x2.309 | G 2 3/4 | 11 | B | 81.534 | 81.100 | 80.055 | 79.621 | 78.576
87.884 |  | G87.884x2.309 | G 3 | 11 | A | 87.884 | 87.450 | 86.405 | 86.188 | 84.926 |  |  | 84.926 | 85.566 | 86.405 | 86.622 | 87.884 |  | 76.2000 | 175.768 | 10.0000
87.884 |  | G87.884x2.309 | G 3 | 11 | B | 87.884 | 87.450 | 86.405 | 85.971 | 84.926
100.330 |  | G100.33x2.309 | G 3 1/2 | 11 | A | 100.330 | 99.896 | 98.851 | 98.634 | 97.372 |  |  | 97.372 | 98.012 | 98.851 | 99.068 | 100.330 |  | 88.9000 | 200.660 | 10.0000
100.330 |  | G100.33x2.309 | G 3 1/2 | 11 | B | 100.330 | 99.896 | 98.851 | 98.417 | 97.372
113.030 |  | G113.03x2.309 | G 4 | 11 | A | 113.030 | 112.596 | 111.551 | 111.334 | 110.072 |  |  | 110.072 | 110.712 | 111.551 | 111.768 | 113.030 |  | 101.6000 | 226.060 | 10.0000
113.030 |  | G113.03x2.309 | G 4 | 11 | B | 113.030 | 112.596 | 111.551 | 111.117 | 110.072
125.730 |  | G125.73x2.309 | G 4 1/2 | 11 | A | 125.730 | 125.296 | 124.251 | 124.034 | 122.772 |  |  | 122.772 | 123.412 | 124.251 | 124.468 | 125.730 |  | 114.3000 | 251.460 | 10.0000
125.730 |  | G125.73x2.309 | G 4 1/2 | 11 | B | 125.730 | 125.296 | 124.251 | 123.817 | 122.772
138.430 |  | G138.43x2.309 | G 5 | 11 | A | 138.430 | 137.996 | 136.951 | 136.734 | 135.472 |  |  | 135.472 | 136.112 | 136.951 | 137.168 | 138.430 |  | 127.0000 | 276.860 | 10.0000
138.430 |  | G138.43x2.309 | G 5 | 11 | B | 138.430 | 137.996 | 136.951 | 136.517 | 135.472
151.130 |  | G151.13x2.309 | G 5 1/2 | 11 | A | 151.130 | 150.696 | 149.651 | 149.434 | 148.172 |  |  | 148.172 | 148.812 | 149.651 | 149.868 | 151.130 |  | 139.7000 | 302.260 | 10.0000
151.130 |  | G151.13x2.309 | G 5 1/2 | 11 | B | 151.130 | 150.696 | 149.651 | 149.217 | 148.172
163.830 |  | G163.83x2.309 | G 6 | 11 | A | 163.830 | 163.396 | 162.351 | 162.134 | 160.872 |  |  | 160.872 | 161.512 | 162.351 | 162.568 | 163.830 |  | 152.4000 | 327.660 | 10.0000
163.830 |  | G163.83x2.309 | G 6 | 11 | B | 163.830 | 163.396 | 162.351 | 161.917 | 160.872

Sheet: JIS Pipe Threads
M Q | JIS Pipe Threads |  | Sort Order -12 |  | External |  |  |  |  |  |  | Internal
 |  |  |  |  |  | Major Dia |  | Pitch Dia |  | Minor Dia |  |  | Minor Dia |  | Pitch Dia |  | Major Dia |  | Tap Drill | Thread Depth | Thread Runouts
Size | Size Suffix | Thread Designation | Custom Thread Designation | TPI | Class | Max | Min | Max | Min | Max | Min | Class | Min | Max | Min | Max | Min | Max | Basic |  | Basic
7.723 |  | G7.723x0.907 | G 1/16 | 28 | A | 7.723 | 7.509 | 7.142 | 7.035 | 6.561 |  |  | 6.561 | 6.834 | 7.142 | 7.249 | 7.723 |  | 1.5875 | 15.446 | 4.5000
7.723 |  | G7.723x0.907 | G 1/16 | 28 | B | 7.723 | 7.509 | 7.142 | 6.928 | 6.561
9.728 |  | G9.728x0.907 | G 1/8 | 28 | A | 9.728 | 9.514 | 9.147 | 9.040 | 8.566 |  |  | 8.566 | 8.848 | 9.147 | 9.254 | 9.728 |  | 3.1750 | 19.456 | 4.5000
9.728 |  | G9.728x0.907 | G 1/8 | 28 | B | 9.728 | 9.514 | 9.147 | 8.933 | 8.566
13.157 |  | G13.157x1.337 | G 1/4 | 19 | A | 13.157 | 12.907 | 12.301 | 12.176 | 11.445 |  |  | 11.445 | 11.89 | 12.301 | 12.426 | 13.157 |  | 6.3500 | 26.314 | 6.5000
13.157 |  | G13.157x1.337 | G 1/4 | 19 | B | 13.157 | 12.907 | 12.301 | 12.051 | 11.445
16.662 |  | G16.662x1.337 | G 3/8 | 19 | A | 16.662 | 16.412 | 15.806 | 15.681 | 14.950 |  |  | 14.95 | 15.395 | 15.806 | 15.931 | 16.662 |  | 9.5250 | 33.324 | 6.5000
16.662 |  | G16.662x1.337 | G 3/8 | 19 | B | 16.662 | 16.412 | 15.806 | 15.556 | 14.950
20.955 |  | G20.955x1.814 | G 1/2 | 14 | A | 20.955 | 20.671 | 19.793 | 19.651 | 18.631 |  |  | 18.631 | 19.172 | 19.793 | 19.935 | 20.955 |  | 12.7000 | 41.910 | 8.5000
20.955 |  | G20.955x1.814 | G 1/2 | 14 | B | 20.955 | 20.671 | 19.793 | 19.509 | 18.631
22.911 |  | G22.911x1.814 | G 5/8 | 14 | A | 22.911 | 22.627 | 21.749 | 21.607 | 20.587 |  |  | 20.587 | 21.128 | 21.749 | 21.891 | 22.911 |  |  | 45.822 | 8.5000
22.911 |  | G22.911x1.814 | G 5/8 | 14 | B | 22.911 | 22.627 | 21.749 | 21.465 | 20.587
26.441 |  | G26.441x1.814 | G 3/4 | 14 | A | 26.441 | 26.157 | 25.279 | 25.137 | 24.117 |  |  | 24.117 | 24.658 | 25.279 | 25.421 | 26.441 |  | 15.8750 | 52.882 | 8.5000
26.441 |  | G26.441x1.814 | G 3/4 | 14 | B | 26.441 | 26.157 | 25.279 | 24.995 | 24.117
30.201 |  | G30.201x1.814 | G 7/8 | 14 | A | 30.201 | 29.917 | 29.039 | 28.897 | 27.877 |  |  | 27.877 | 28.418 | 29.039 | 29.181 | 30.201 |  | 22.2250 | 60.402 | 8.8000
30.201 |  | G30.201x1.814 | G 7/8 | 14 | B | 30.201 | 29.917 | 29.039 | 28.755 | 27.877
33.249 |  | G33.249x2.309 | G 1 | 11 | A | 33.249 | 32.889 | 31.770 | 31.590 | 30.291 |  |  | 30.291 | 30.931 | 31.77 | 31.95 | 33.249 |  | 25.4000 | 66.498 | 10.0000
33.249 |  | G33.249x2.309 | G 1 | 11 | B | 33.249 | 32.889 | 31.770 | 31.410 | 30.291
37.897 |  | G37.897x2.309 | G 1 1/8 | 11 | A | 37.897 | 37.537 | 36.418 | 36.238 | 34.939 |  |  | 34.939 | 35.579 | 36.418 | 36.598 | 37.897 |  | 28.5750 | 75.794 | 10.0000
37.897 |  | G37.897x2.309 | G 1 1/8 | 11 | B | 37.897 | 37.537 | 36.418 | 36.058 | 34.939
41.910 |  | G41.91x2.309 | G 1 1/4 | 11 | A | 41.910 | 41.550 | 40.431 | 40.251 | 38.952 |  |  | 38.952 | 39.592 | 40.431 | 40.611 | 41.910 |  | 31.7500 | 83.820 | 10.0000
41.910 |  | G41.91x2.309 | G 1 1/4 | 11 | B | 41.910 | 41.550 | 40.431 | 40.071 | 38.952
47.803 |  | G47.803x2.309 | G 1 1/2 | 11 | A | 47.803 | 47.443 | 46.324 | 46.144 | 44.845 |  |  | 44.845 | 45.485 | 46.324 | 46.504 | 47.803 |  | 38.1000 | 95.606 | 10.0000
47.803 |  | G47.803x2.309 | G 1 1/2 | 11 | B | 47.803 | 47.443 | 46.324 | 45.964 | 44.845
53.746 |  | G53.746x2.309 | G 1 3/4 | 11 | A | 53.746 | 53.386 | 52.267 | 52.087 | 50.788 |  |  | 50.788 | 51.428 | 52.267 | 52.447 | 53.746 |  | 44.4500 | 107.492 | 10.0000
53.746 |  | G53.746x2.309 | G 1 3/4 | 11 | B | 53.746 | 53.386 | 52.267 | 51.907 | 50.788
59.614 |  | G59.614x2.309 | G 2 | 11 | A | 59.614 | 59.254 | 58.135 | 57.955 | 56.656 |  |  | 56.656 | 57.296 | 58.135 | 58.315 | 59.614 |  | 50.8000 | 119.228 | 10.0000
59.614 |  | G59.614x2.309 | G 2 | 11 | B | 59.614 | 59.254 | 58.135 | 57.775 | 56.656
65.710 |  | G65.71x2.309 | G 2 1/4 | 11 | A | 65.710 | 65.276 | 64.231 | 64.014 | 62.752 |  |  | 62.752 | 63.392 | 64.231 | 64.448 | 65.710 |  | 57.1500 | 131.420 | 10.0000
65.710 |  | G65.71x2.309 | G 2 1/4 | 11 | B | 65.710 | 65.276 | 64.231 | 63.797 | 62.752
75.184 |  | G75.184x2.309 | G 2 1/2 | 11 | A | 75.184 | 74.750 | 73.705 | 73.488 | 72.226 |  |  | 72.226 | 72.866 | 73.705 | 73.922 | 75.184 |  |  | 150.368 | 10.0000
75.184 |  | G75.184x2.309 | G 2 1/2 | 11 | B | 75.184 | 74.750 | 73.705 | 73.271 | 72.226
81.534 |  | G81.534x2.309 | G 2 3/4 | 11 | A | 81.534 | 81.100 | 80.055 | 79.838 | 78.576 |  |  | 78.576 | 79.216 | 80.055 | 80.272 | 81.534 |  | 69.8500 | 163.068 | 10.0000
81.534 |  | G81.534x2.309 | G 2 3/4 | 11 | B | 81.534 | 81.100 | 80.055 | 79.621 | 78.576
87.884 |  | G87.884x2.309 | G 3 | 11 | A | 87.884 | 87.450 | 86.405 | 86.188 | 84.926 |  |  | 84.926 | 85.566 | 86.405 | 86.622 | 87.884 |  | 76.2000 | 175.768 | 10.0000
87.884 |  | G87.884x2.309 | G 3 | 11 | B | 87.884 | 87.450 | 86.405 | 85.971 | 84.926
100.330 |  | G100.33x2.309 | G 3 1/2 | 11 | A | 100.330 | 99.896 | 98.851 | 98.634 | 97.372 |  |  | 97.372 | 98.012 | 98.851 | 99.068 | 100.330 |  | 88.9000 | 200.660 | 10.0000
100.330 |  | G100.33x2.309 | G 3 1/2 | 11 | B | 100.330 | 99.896 | 98.851 | 98.417 | 97.372
113.030 |  | G113.03x2.309 | G 4 | 11 | A | 113.030 | 112.596 | 111.551 | 111.334 | 110.072 |  |  | 110.072 | 110.712 | 111.551 | 111.768 | 113.030 |  | 101.6000 | 226.060 | 10.0000
113.030 |  | G113.03x2.309 | G 4 | 11 | B | 113.030 | 112.596 | 111.551 | 111.117 | 110.072
125.730 |  | G125.73x2.309 | G 4 1/2 | 11 | A | 125.730 | 125.296 | 124.251 | 124.034 | 122.772 |  |  | 122.772 | 123.412 | 124.251 | 124.468 | 125.730 |  | 114.3000 | 251.460 | 10.0000
125.730 |  | G125.73x2.309 | G 4 1/2 | 11 | B | 125.730 | 125.296 | 124.251 | 123.817 | 122.772
138.430 |  | G138.43x2.309 | G 5 | 11 | A | 138.430 | 137.996 | 136.951 | 136.734 | 135.472 |  |  | 135.472 | 136.112 | 136.951 | 137.168 | 138.430 |  | 127.0000 | 276.860 | 10.0000
138.430 |  | G138.43x2.309 | G 5 | 11 | B | 138.430 | 137.996 | 136.951 | 136.517 | 135.472
151.130 |  | G151.13x2.309 | G 5 1/2 | 11 | A | 151.130 | 150.696 | 149.651 | 149.434 | 148.172 |  |  | 148.172 | 148.812 | 149.651 | 149.868 | 151.130 |  | 139.7000 | 302.260 | 10.0000
151.130 |  | G151.13x2.309 | G 5 1/2 | 11 | B | 151.130 | 150.696 | 149.651 | 149.217 | 148.172
163.830 |  | G163.83x2.309 | G 6 | 11 | A | 163.830 | 163.396 | 162.351 | 162.134 | 160.872 |  |  | 160.872 | 161.512 | 162.351 | 162.568 | 163.830 |  | 152.4000 | 327.660 | 10.0000
163.830 |  | G163.83x2.309 | G 6 | 11 | B | 163.830 | 163.396 | 162.351 | 161.917 | 160.872

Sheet: DIN Pipe Threads
M Q | DIN Pipe Threads |  | Sort Order - 18 |  | External |  |  |  |  |  |  | Internal
 |  |  |  |  |  | Major Dia |  | Pitch Dia |  | Minor Dia |  |  | Minor Dia |  | Pitch Dia |  | Major Dia |  | Tap Drill | Thread Depth | Thread Runouts
Size | Size Suffix | Thread Designation | Custom Thread Designation | TPI | Class | Max | Min | Max | Min | Max | Min | Class | Min | Max | Min | Max | Min | Max | Basic
7.723 |  | G7.723x0.907 | G 1/16 | 28 | A | 7.723 | 7.509 | 7.142 | 7.035 | 6.561 |  |  | 6.561 | 6.834 | 7.142 | 7.249 | 7.723 |  | 1.5875 | 15.446 | 4.5000
7.723 |  | G7.723x0.907 | G 1/16 | 28 | B | 7.723 | 7.509 | 7.142 | 6.928 | 6.561
9.728 |  | G9.728x0.907 | G 1/8 | 28 | A | 9.728 | 9.514 | 9.147 | 9.040 | 8.566 |  |  | 8.566 | 8.848 | 9.147 | 9.254 | 9.728 |  | 3.1750 | 19.456 | 4.5000
9.728 |  | G9.728x0.907 | G 1/8 | 28 | B | 9.728 | 9.514 | 9.147 | 8.933 | 8.566
13.157 |  | G13.157x1.337 | G 1/4 | 19 | A | 13.157 | 12.907 | 12.301 | 12.176 | 11.445 |  |  | 11.445 | 11.89 | 12.301 | 12.426 | 13.157 |  | 6.3500 | 26.314 | 6.5000
13.157 |  | G13.157x1.337 | G 1/4 | 19 | B | 13.157 | 12.907 | 12.301 | 12.051 | 11.445
16.662 |  | G16.662x1.337 | G 3/8 | 19 | A | 16.662 | 16.412 | 15.806 | 15.681 | 14.950 |  |  | 14.95 | 15.395 | 15.806 | 15.931 | 16.662 |  | 9.5250 | 33.324 | 6.5000
16.662 |  | G16.662x1.337 | G 3/8 | 19 | B | 16.662 | 16.412 | 15.806 | 15.556 | 14.950
20.955 |  | G20.955x1.814 | G 1/2 | 14 | A | 20.955 | 20.671 | 19.793 | 19.651 | 18.631 |  |  | 18.631 | 19.172 | 19.793 | 19.935 | 20.955 |  | 12.7000 | 41.910 | 8.5000
20.955 |  | G20.955x1.814 | G 1/2 | 14 | B | 20.955 | 20.671 | 19.793 | 19.509 | 18.631
22.911 |  | G22.911x1.814 | G 5/8 | 14 | A | 22.911 | 22.627 | 21.749 | 21.607 | 20.587 |  |  | 20.587 | 21.128 | 21.749 | 21.891 | 22.911 |  |  | 45.822 | 8.5000
22.911 |  | G22.911x1.814 | G 5/8 | 14 | B | 22.911 | 22.627 | 21.749 | 21.465 | 20.587
26.441 |  | G26.441x1.814 | G 3/4 | 14 | A | 26.441 | 26.157 | 25.279 | 25.137 | 24.117 |  |  | 24.117 | 24.658 | 25.279 | 25.421 | 26.441 |  | 15.8750 | 52.882 | 8.5000
26.441 |  | G26.441x1.814 | G 3/4 | 14 | B | 26.441 | 26.157 | 25.279 | 24.995 | 24.117
30.201 |  | G30.201x1.814 | G 7/8 | 14 | A | 30.201 | 29.917 | 29.039 | 28.897 | 27.877 |  |  | 27.877 | 28.418 | 29.039 | 29.181 | 30.201 |  | 22.2250 | 60.402 | 8.5000
30.201 |  | G30.201x1.814 | G 7/8 | 14 | B | 30.201 | 29.917 | 29.039 | 28.755 | 27.877
33.249 |  | G33.249x2.309 | G 1 | 11 | A | 33.249 | 32.889 | 31.770 | 31.590 | 30.291 |  |  | 30.291 | 30.931 | 31.77 | 31.95 | 33.249 |  | 25.4000 | 66.498 | 10.5000
33.249 |  | G33.249x2.309 | G 1 | 11 | B | 33.249 | 32.889 | 31.770 | 31.410 | 30.291
37.897 |  | G37.897x2.309 | G 1 1/8 | 11 | A | 37.897 | 37.537 | 36.418 | 36.238 | 34.939 |  |  | 34.939 | 35.579 | 36.418 | 36.598 | 37.897 |  | 28.5750 | 75.794 | 10.5000
37.897 |  | G37.897x2.309 | G 1 1/8 | 11 | B | 37.897 | 37.537 | 36.418 | 36.058 | 34.939
41.910 |  | G41.91x2.309 | G 1 1/4 | 11 | A | 41.910 | 41.550 | 40.431 | 40.251 | 38.952 |  |  | 38.952 | 39.592 | 40.431 | 40.611 | 41.910 |  | 31.7500 | 83.820 | 10.5000
41.910 |  | G41.91x2.309 | G 1 1/4 | 11 | B | 41.910 | 41.550 | 40.431 | 40.071 | 38.952
47.803 |  | G47.803x2.309 | G 1 1/2 | 11 | A | 47.803 | 47.443 | 46.324 | 46.144 | 44.845 |  |  | 44.845 | 45.485 | 46.324 | 46.504 | 47.803 |  | 38.1000 | 95.606 | 10.5000
47.803 |  | G47.803x2.309 | G 1 1/2 | 11 | B | 47.803 | 47.443 | 46.324 | 45.964 | 44.845
53.746 |  | G53.746x2.309 | G 1 3/4 | 11 | A | 53.746 | 53.386 | 52.267 | 52.087 | 50.788 |  |  | 50.788 | 51.428 | 52.267 | 52.447 | 53.746 |  | 44.4500 | 107.492 | 10.5000
53.746 |  | G53.746x2.309 | G 1 3/4 | 11 | B | 53.746 | 53.386 | 52.267 | 51.907 | 50.788
59.614 |  | G59.614x2.309 | G 2 | 11 | A | 59.614 | 59.254 | 58.135 | 57.955 | 56.656 |  |  | 56.656 | 57.296 | 58.135 | 58.315 | 59.614 |  | 50.8000 | 119.228 | 10.5000
59.614 |  | G59.614x2.309 | G 2 | 11 | B | 59.614 | 59.254 | 58.135 | 57.775 | 56.656
65.710 |  | G65.71x2.309 | G 2 1/4 | 11 | A | 65.710 | 65.276 | 64.231 | 64.014 | 62.752 |  |  | 62.752 | 63.392 | 64.231 | 64.448 | 65.710 |  | 57.1500 | 131.420 | 10.5000
65.710 |  | G65.71x2.309 | G 2 1/4 | 11 | B | 65.710 | 65.276 | 64.231 | 63.797 | 62.752
75.184 |  | G75.184x2.309 | G 2 1/2 | 11 | A | 75.184 | 74.750 | 73.705 | 73.488 | 72.226 |  |  | 72.226 | 72.866 | 73.705 | 73.922 | 75.184 |  |  | 150.368 | 10.5000
75.184 |  | G75.184x2.309 | G 2 1/2 | 11 | B | 75.184 | 74.750 | 73.705 | 73.271 | 72.226
81.534 |  | G81.534x2.309 | G 2 3/4 | 11 | A | 81.534 | 81.100 | 80.055 | 79.838 | 78.576 |  |  | 78.576 | 79.216 | 80.055 | 80.272 | 81.534 |  | 69.8500 | 163.068 | 10.5000
81.534 |  | G81.534x2.309 | G 2 3/4 | 11 | B | 81.534 | 81.100 | 80.055 | 79.621 | 78.576
87.884 |  | G87.884x2.309 | G 3 | 11 | A | 87.884 | 87.450 | 86.405 | 86.188 | 84.926 |  |  | 84.926 | 85.566 | 86.405 | 86.622 | 87.884 |  | 76.2000 | 175.768 | 10.5000
87.884 |  | G87.884x2.309 | G 3 | 11 | B | 87.884 | 87.450 | 86.405 | 85.971 | 84.926
100.330 |  | G100.33x2.309 | G 3 1/2 | 11 | A | 100.330 | 99.896 | 98.851 | 98.634 | 97.372 |  |  | 97.372 | 98.012 | 98.851 | 99.068 | 100.330 |  | 88.9000 | 200.660 | 10.5000
100.330 |  | G100.33x2.309 | G 3 1/2 | 11 | B | 100.330 | 99.896 | 98.851 | 98.417 | 97.372
113.030 |  | G113.03x2.309 | G 4 | 11 | A | 113.030 | 112.596 | 111.551 | 111.334 | 110.072 |  |  | 110.072 | 110.712 | 111.551 | 111.768 | 113.030 |  | 101.6000 | 226.060 | 10.5000
113.030 |  | G113.03x2.309 | G 4 | 11 | B | 113.030 | 112.596 | 111.551 | 111.117 | 110.072
125.730 |  | G125.73x2.309 | G 4 1/2 | 11 | A | 125.730 | 125.296 | 124.251 | 124.034 | 122.772 |  |  | 122.772 | 123.412 | 124.251 | 124.468 | 125.730 |  | 114.3000 | 251.460 | 10.5000
125.730 |  | G125.73x2.309 | G 4 1/2 | 11 | B | 125.730 | 125.296 | 124.251 | 123.817 | 122.772
138.430 |  | G138.43x2.309 | G 5 | 11 | A | 138.430 | 137.996 | 136.951 | 136.734 | 135.472 |  |  | 135.472 | 136.112 | 136.951 | 137.168 | 138.430 |  | 127.0000 | 276.860 | 10.5000
138.430 |  | G138.43x2.309 | G 5 | 11 | B | 138.430 | 137.996 | 136.951 | 136.517 | 135.472
151.130 |  | G151.13x2.309 | G 5 1/2 | 11 | A | 151.130 | 150.696 | 149.651 | 149.434 | 148.172 |  |  | 148.172 | 148.812 | 149.651 | 149.868 | 151.130 |  | 139.7000 | 302.260 | 10.5000
151.130 |  | G151.13x2.309 | G 5 1/2 | 11 | B | 151.130 | 150.696 | 149.651 | 149.217 | 148.172
163.830 |  | G163.83x2.309 | G 6 | 11 | A | 163.830 | 163.396 | 162.351 | 162.134 | 160.872 |  |  | 160.872 | 161.512 | 162.351 | 162.568 | 163.830 |  | 152.4000 | 327.660 | 10.5000
163.830 |  | G163.83x2.309 | G 6 | 11 | B | 163.830 | 163.396 | 162.351 | 161.917 | 160.872

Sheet: BSP Pipe Threads
M Q | BSP Pipe Threads |  | Sort Order - 19 |  | External |  |  |  |  |  |  | Internal
 |  |  |  |  |  | Major Dia |  | Pitch Dia |  | Minor Dia |  |  | Minor Dia |  | Pitch Dia |  | Major Dia |  | Tap Drill | Thread Depth | Thread Runouts
Size | Size Suffix | Thread Designation | Custom Thread Designation | TPI | Class | Max | Min | Max | Min | Max | Min | Class | Min | Max | Min | Max | Min | Max | Basic |  | Basic
1/16 |  | G 1/16-28 | G 1/16-28 | 28 | A | 7.723 | 7.509 | 7.142 | 7.035 | 6.561 |  |  | 6.561 | 6.834 | 7.142 | 7.249 | 7.723 |  | 6.6000 | 15.4460 | 4.5000
1/16 |  | G 1/16-28 | G 1/16-28 | 28 | B | 7.723 | 7.509 | 7.142 | 7.035 | 6.561
1/8 |  | G 1/8-28 | G 1/8-28 | 28 | A | 9.728 | 9.514 | 9.147 | 9.040 | 8.566 |  |  | 8.566 | 8.848 | 9.147 | 9.254 | 9.728 |  | 8.7300 | 19.4560 | 4.5000
1/8 |  | G 1/8-28 | G 1/8-28 | 28 | B | 9.728 | 9.514 | 9.147 | 9.040 | 8.566
1/4 |  | G 1/4-19 | G 1/4-19 | 19 | A | 13.157 | 12.907 | 12.301 | 12.176 | 11.445 |  |  | 11.445 | 11.89 | 12.301 | 12.426 | 13.157 |  | 11.8000 | 26.3140 | 6.5000
1/4 |  | G 1/4-19 | G 1/4-19 | 19 | B | 13.157 | 12.907 | 12.301 | 12.176 | 11.445
3/8 |  | G 3/8-19 | G 3/8-19 | 19 | A | 16.662 | 16.412 | 15.806 | 15.681 | 14.950 |  |  | 14.95 | 15.395 | 15.806 | 15.931 | 16.662 |  | 15.2500 | 33.3240 | 6.5000
3/8 |  | G 3/8-19 | G 3/8-19 | 19 | B | 16.662 | 16.412 | 15.806 | 15.681 | 14.950
1/2 |  | G 1/2-14 | G 1/2-14 | 14 | A | 20.955 | 20.671 | 19.793 | 19.651 | 18.631 |  |  | 18.631 | 19.172 | 19.793 | 19.935 | 20.955 |  | 19.0500 | 41.9100 | 8.5000
1/2 |  | G 1/2-14 | G 1/2-14 | 14 | B | 20.955 | 20.671 | 19.793 | 19.651 | 18.631
5/8 |  | G 5/8-14 | G 5/8-14 | 14 | A | 22.911 | 22.627 | 21.749 | 21.607 | 20.587 |  |  | 20.587 | 21.128 | 21.749 | 21.891 | 22.911 |  | 21.0000 | 45.8220 | 8.5000
5/8 |  | G 5/8-14 | G 5/8-14 | 14 | B | 22.911 | 22.627 | 21.749 | 21.607 | 20.587
3/4 |  | G 3/4-14 | G 3/4-14 | 14 | A | 26.441 | 26.157 | 25.279 | 25.137 | 24.117 |  |  | 24.117 | 24.658 | 25.279 | 25.421 | 26.441 |  | 24.5000 | 52.8820 | 8.5000
3/4 |  | G 3/4-14 | G 3/4-14 | 14 | B | 26.441 | 26.157 | 25.279 | 25.137 | 24.117
7/8 |  | G 7/8-14 | G 7/8-14 | 14 | A | 30.201 | 29.917 | 29.039 | 28.897 | 27.877 |  |  | 27.877 | 28.418 | 29.039 | 29.181 | 30.201 |  | 28.2500 | 60.4020 | 8.5000
7/8 |  | G 7/8-14 | G 7/8-14 | 14 | B | 30.201 | 29.917 | 29.039 | 28.897 | 27.877
1 |  | G 1-11 | G 1-11 | 11 | A | 33.249 | 32.889 | 31.770 | 31.590 | 30.291 |  |  | 30.291 | 30.931 | 31.77 | 31.95 | 33.249 |  | 30.7500 | 66.4980 | 10.0000
1 |  | G 1-11 | G 1-11 | 11 | B | 33.249 | 32.889 | 31.770 | 31.590 | 30.291
1 1/4 |  | G 1 1/4-11 | G 1 1/4-11 | 11 | A | 41.910 | 41.550 | 40.431 | 40.251 | 38.952 |  |  | 38.952 | 39.592 | 40.431 | 40.611 | 41.910 |  | 39.5000 | 83.8200 | 10.0000
1 1/4 |  | G 1 1/4-11 | G 1 1/4-11 | 11 | B | 41.910 | 41.550 | 40.431 | 40.251 | 38.952
1 1/2 |  | G 1 1/2-11 | G 1 1/2-11 | 11 | A | 47.803 | 47.443 | 46.324 | 46.144 | 44.845 |  |  | 44.845 | 45.485 | 46.324 | 46.504 | 47.803 |  | 45.5000 | 95.6060 | 10.0000
1 1/2 |  | G 1 1/2-11 | G 1 1/2-11 | 11 | B | 47.803 | 47.443 | 46.324 | 46.144 | 44.845
1 3/4 |  | G 1 3/4-11 | G 1 3/4-11 | 11 | A | 53.746 | 53.386 | 52.267 | 52.087 | 50.788 |  |  | 50.788 | 51.428 | 52.267 | 52.447 | 53.746 |  | 51.0000 | 107.4920 | 10.0000
1 3/4 |  | G 1 3/4-11 | G 1 3/4-11 | 11 | B | 53.746 | 53.386 | 52.267 | 52.087 | 50.788
2 |  | G 2-11 | G 2-11 | 11 | A | 59.614 | 59.254 | 58.135 | 57.955 | 56.656 |  |  | 56.656 | 57.296 | 58.135 | 58.315 | 59.614 |  | 57.0000 | 119.2280 | 10.0000
2 |  | G 2-11 | G 2-11 | 11 | B | 59.614 | 59.254 | 58.135 | 57.955 | 56.656
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

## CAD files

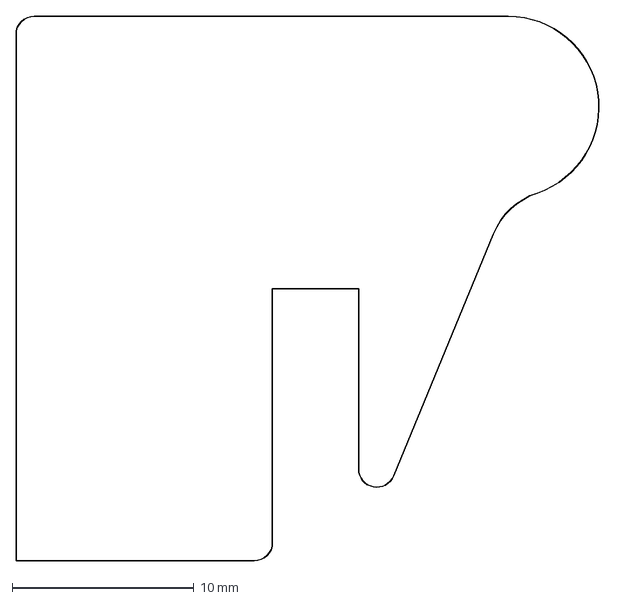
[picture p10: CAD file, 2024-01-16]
mechanics/export/V1-bis/nez.dxf
32.4 x 30.0 mm

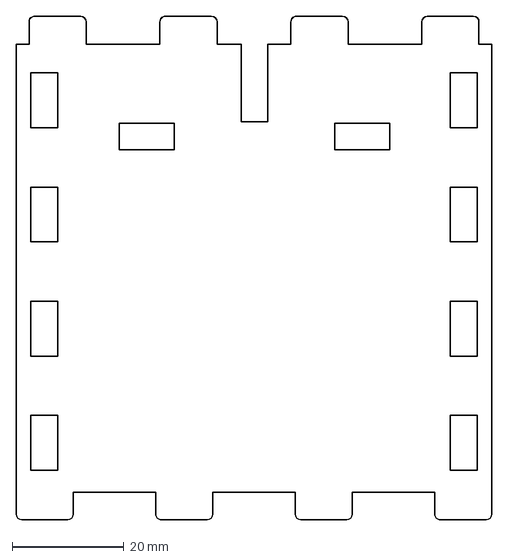
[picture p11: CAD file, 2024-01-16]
mechanics/export/V2/devant.dxf
85.0 x 90.0 mm

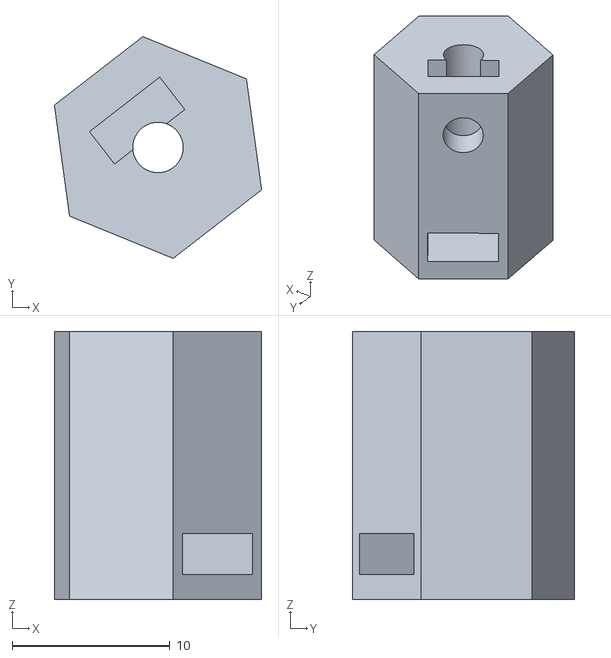
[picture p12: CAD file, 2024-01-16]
mechanics/wheel_to_motor.stl
13.1 x 14.1 x 17.0

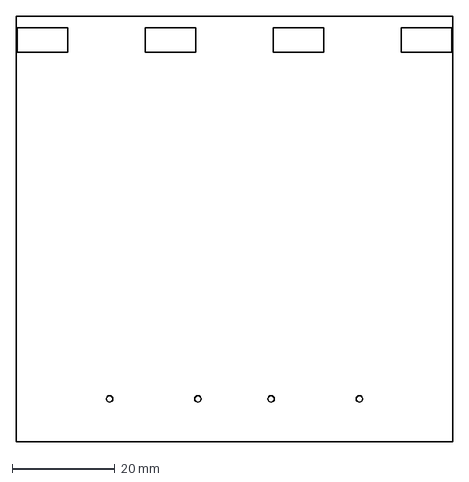
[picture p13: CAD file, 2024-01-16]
mechanics/export/V1-bis/tete.dxf
85.0 x 82.9 mm

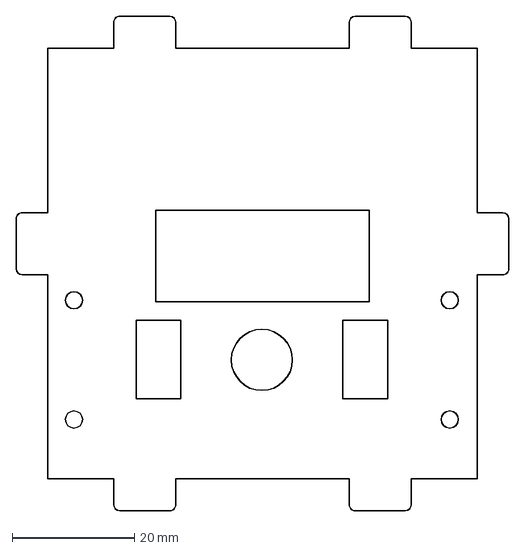
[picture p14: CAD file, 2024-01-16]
mechanics/export/V2/etage.dxf
80.6 x 80.9 mm

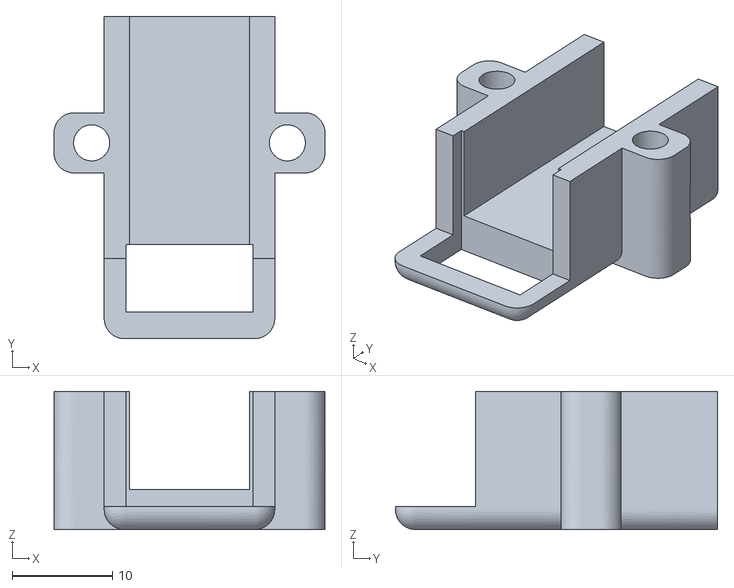
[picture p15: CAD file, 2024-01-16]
mechanics/motorbox_unique.stl
27.0 x 32.1 x 13.8

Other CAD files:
mechanics/new_tiny/cubi.dwg
mechanics/new_tiny/modules/attrape_ball.dwg
mechanics/pendulum/Templates/English/am_ansi.dwg
mechanics/pendulum/Templates/Metric/am_iso.dwg
mechanics/pendulum/Templates/Standard.dwg
mechanics/tiny/Templates/English/am_ansi.dwg
mechanics/tiny/Templates/Metric/GB.dwg
mechanics/tiny/Templates/Standard.dwg
mechanics/new_tiny/modules/for_metabois.dwg
mechanics/pendulum/Templates/English/ANSI (in).dwg
mechanics/pendulum/Templates/Metric/GB.dwg
mechanics/tiny/Templates/English/ANSI (in).dwg
mechanics/OldVersions/base2.0002.ipt
mechanics/OldVersions/capot.0002.ipt
mechanics/OldVersions/motorbox_bottom.0012.ipt
mechanics/OldVersions/wheel_to_motor.0012.ipt
mechanics/base.iam
mechanics/base.ipt
mechanics/battery.ipt
mechanics/board_rev0.ipt
mechanics/export/V0/base.dxf
mechanics/export/V0/cote.dxf
mechanics/export/V0/derriere.dxf
mechanics/export/V0/devant.dxf
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

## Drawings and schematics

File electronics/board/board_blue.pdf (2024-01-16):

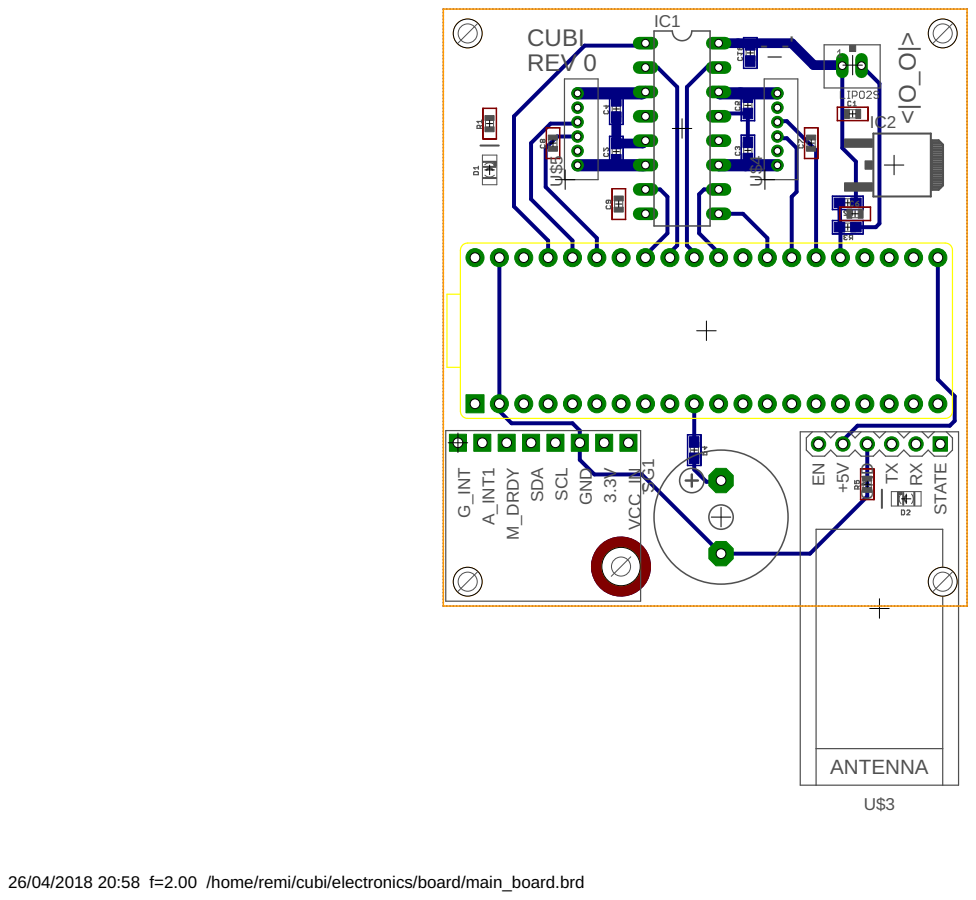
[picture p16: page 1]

26/04/2018 20:58 f=2.00 /home/remi/cubi/electronics/board/main_board.brd

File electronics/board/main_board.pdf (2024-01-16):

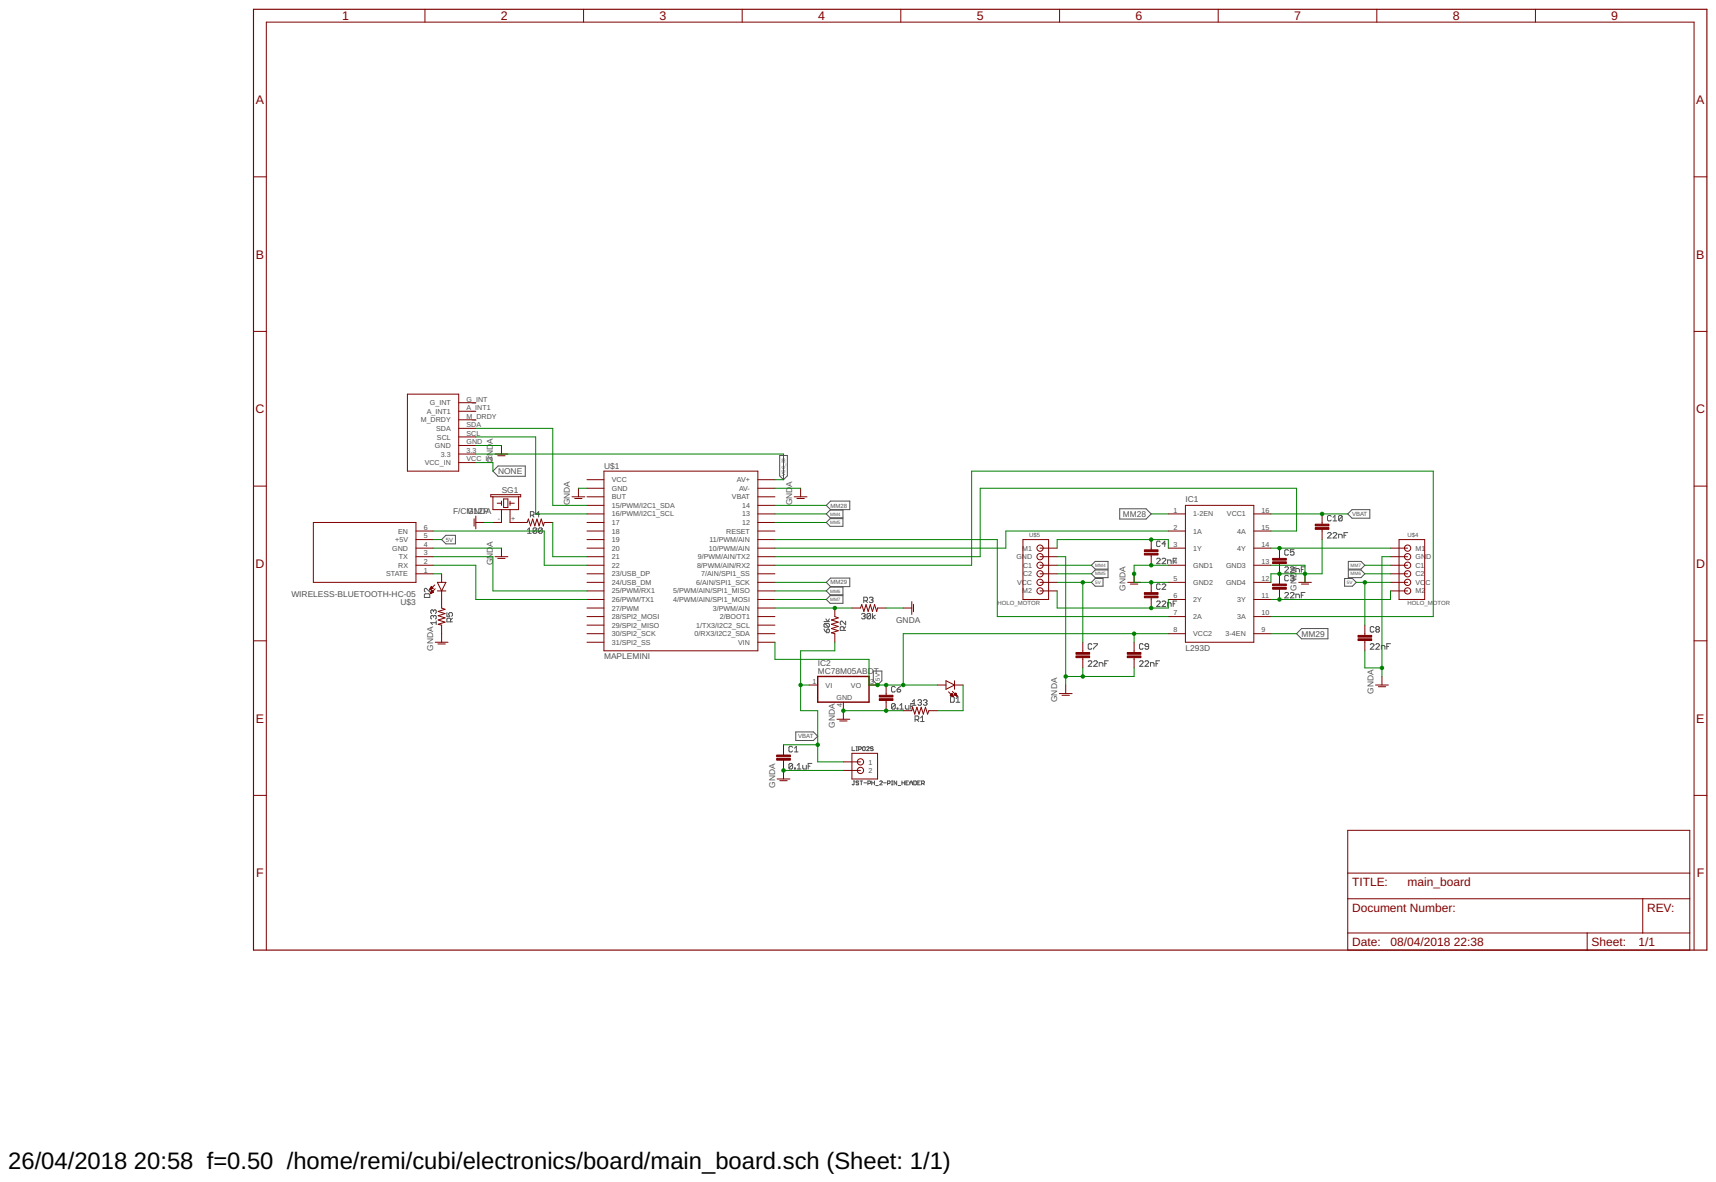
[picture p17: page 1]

11/PWM/AIN
10/PWM/AIN
9/PWM/AIN/TX2
8/PWM/AIN/RX2
7/AIN/SPI1_SS
6/AIN/SPI1_SCK
5/PWM/AIN/SPI1_MISO
4/PWM/AIN/SPI1_MOSI 3/PWM/AIN

26/04/2018 20:58 f=0.50 /home/remi/cubi/electronics/board/main_board.sch (Sheet: 1/1)

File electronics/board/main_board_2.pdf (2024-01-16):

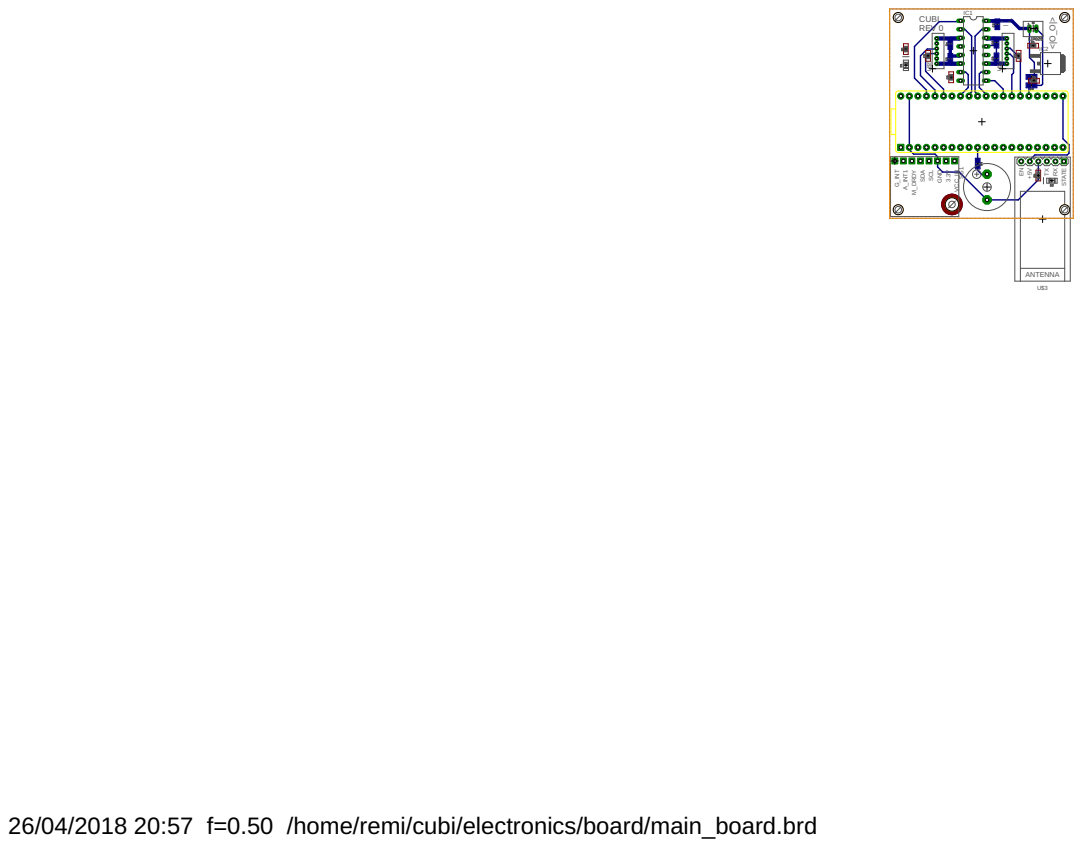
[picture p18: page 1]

26/04/2018 20:57 f=0.50 /home/remi/cubi/electronics/board/main_board.brd

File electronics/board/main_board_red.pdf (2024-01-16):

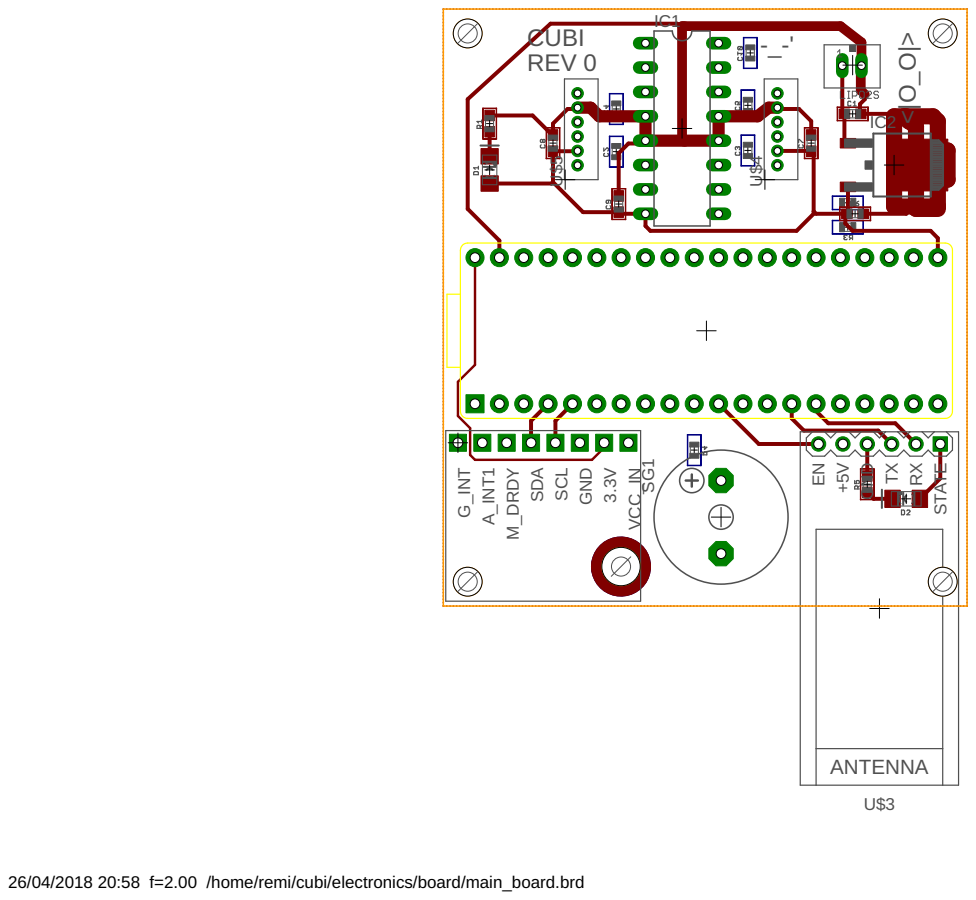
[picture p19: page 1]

26/04/2018 20:58 f=2.00 /home/remi/cubi/electronics/board/main_board.brd

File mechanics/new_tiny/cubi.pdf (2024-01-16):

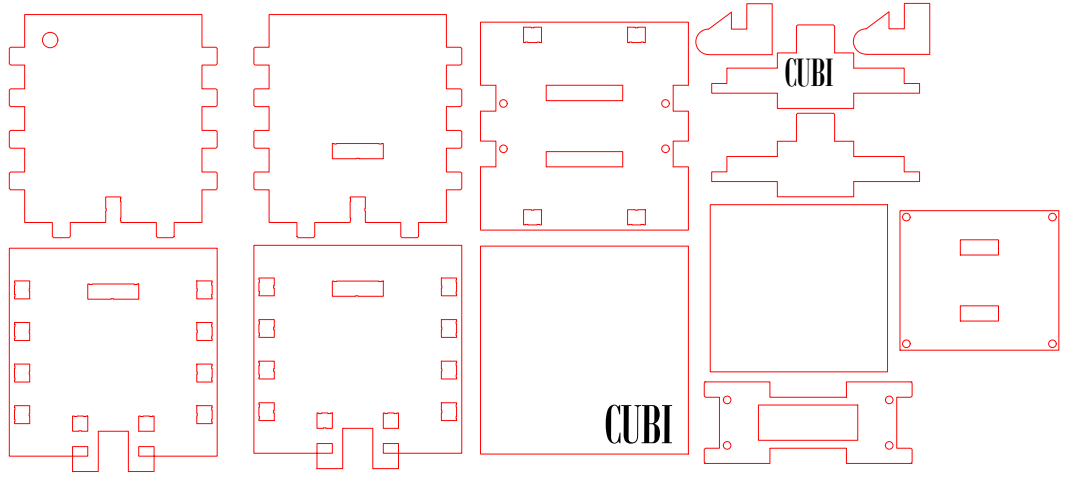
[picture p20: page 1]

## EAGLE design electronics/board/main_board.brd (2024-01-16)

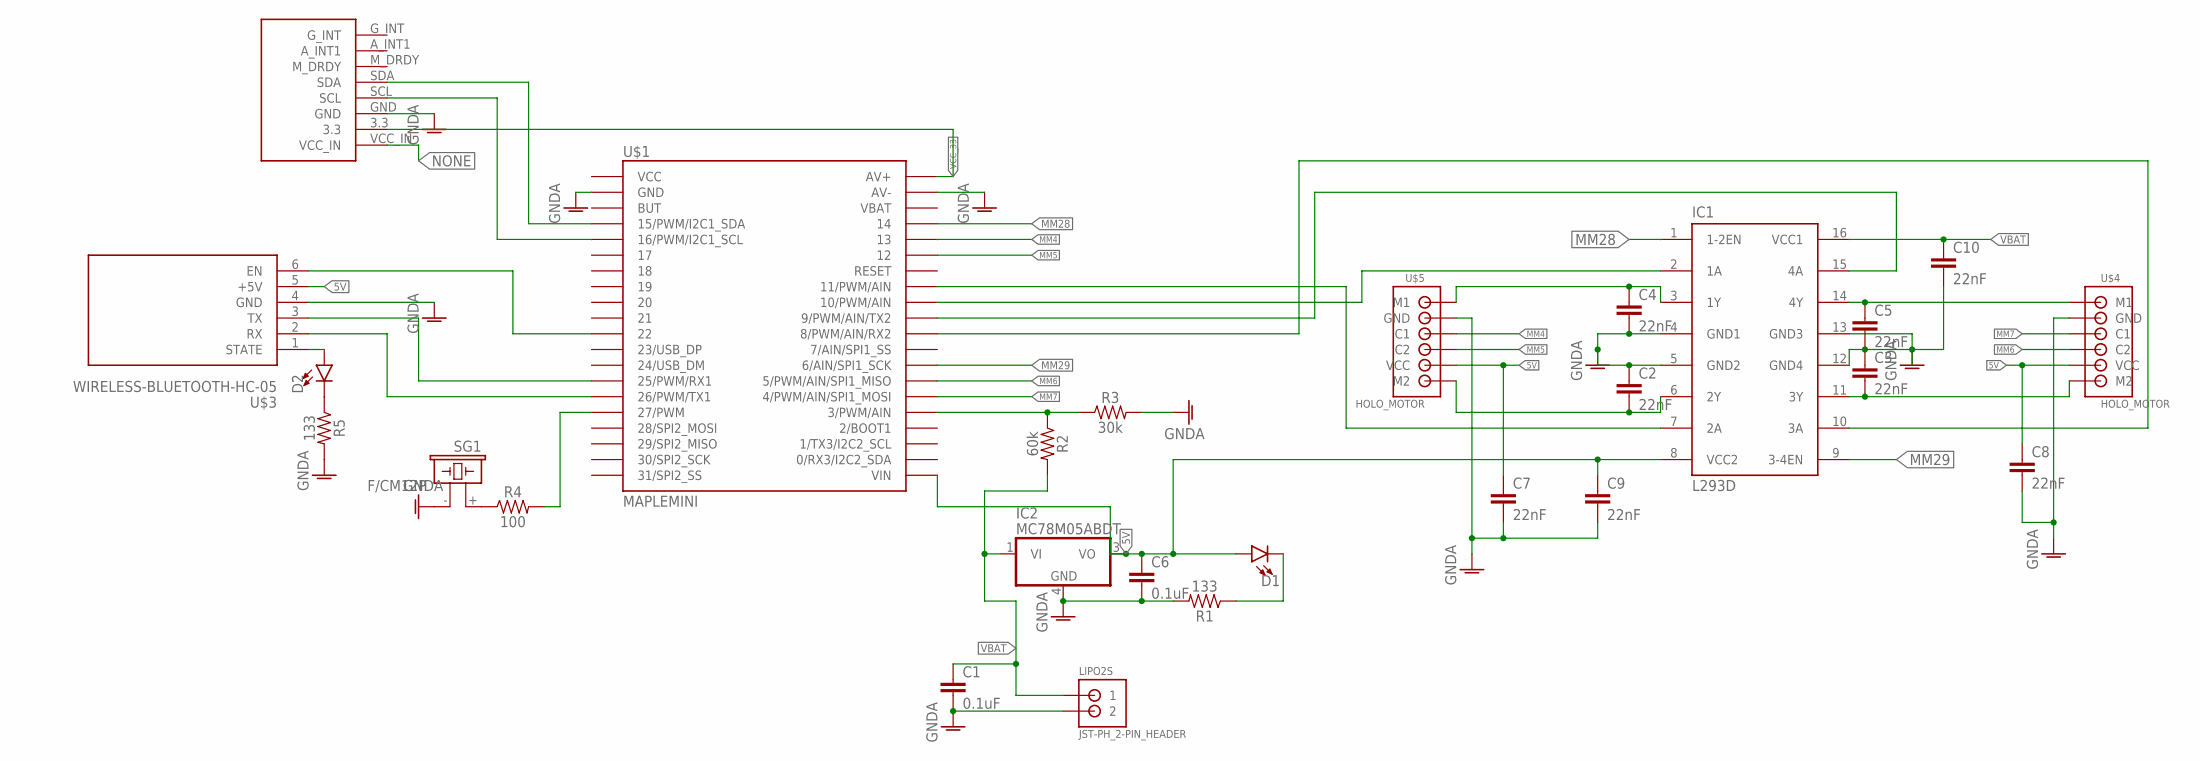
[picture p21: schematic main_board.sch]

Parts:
C1, C6: 0.1uF; 0603
C2, C3, C4, C5, C7, C8, C9, C10: 22nF; 0603
D1, D2: LED-FKIT-1206; FKIT-LED-1206
IC1: L293D; DIL16
IC2: MC78M05ABDT; DPACK_3
LIPO2S: JST-PH_2-PIN_HEADER; JST_B2B-PH_HEADER
R1, R5: 133; 0603
R2: 60k; 0603
R3: 30k; 0603
R4: 100; 0603
SG1: F/CM12P
U$1: MAPLEMINI; 20-DIP
U$3: WIRELESS-BLUETOOTH-HC-05
U$4, U$5: HOLO_MOTOR
U$6: GY-85

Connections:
5V: C6.1, C7.1, C8.1, C9.1, D1.A, IC1.8 (VCC2), IC2.3 (VO), U$1.21 (VIN), U$3.5 (+5V), U$4.5 (VCC), U$5.5 (VCC)
GNDA: C1.2, C2.1, C3.1, C4.2, C5.2, C6.2, C7.2, C8.2, C9.2, C10.2, IC1.4 (GND1), IC1.5 (GND2), IC1.12 (GND4), IC1.13 (GND3), IC2.4 (GND), LIPO2S.P2 (2), R1.2, R3.2, R5.2, SG1.- (2), U$1.2 (GND), U$1.39 (AV-), U$3.4 (GND), U$4.2 (GND), U$5.2 (GND), U$6.GND
MM4: U$1.36 (13), U$5.3 (C1)
MM5: U$1.35 (12), U$5.4 (C2)
MM6: U$1.27 (5/PWM/AIN/SPI1_MISO), U$4.4 (C2)
MM7: U$1.26 (4/PWM/AIN/SPI1_MOSI), U$4.3 (C1)
MM28: IC1.1 (1-2EN), U$1.37 (14)
MM29: IC1.9 (3-4EN), U$1.28 (6/AIN/SPI1_SCK)
unnamed: D1.C, R1.1
unnamed: R4.2, U$1.16 (27/PWM)
unnamed: IC1.10 (3A), U$1.30 (8/PWM/AIN/RX2)
unnamed: U$1.15 (26/PWM/TX1), U$3.2 (RX)
unnamed: U$1.14 (25/PWM/RX1), U$3.3 (TX)
unnamed: U$1.5 (16/PWM/I2C1_SCL), U$6.SCL
unnamed: C5.1, IC1.14 (4Y), U$4.1 (M1)
unnamed: U$1.11 (22), U$3.6 (EN)
unnamed: R2.1, R3.1, U$1.25 (3/PWM/AIN)
unnamed: IC1.7 (2A), U$1.33 (11/PWM/AIN)
unnamed: IC1.2 (1A), U$1.32 (10/PWM/AIN)
unnamed: IC1.15 (4A), U$1.31 (9/PWM/AIN/TX2)
unnamed: U$1.4 (15/PWM/I2C1_SDA), U$6.SDA
unnamed: R4.1, SG1.+ (1)
unnamed: C4.1, IC1.3 (1Y), U$5.1 (M1)
unnamed: C3.2, IC1.11 (3Y), U$4.6 (M2)
unnamed: C2.2, IC1.6 (2Y), U$5.6 (M2)
unnamed: D2.A, U$3.1 (STATE)
unnamed: D2.C, R5.1
NONE: U$6.VCC_IN
VBAT: C1.1, C10.1, IC1.16 (VCC1), IC2.1 (VI), LIPO2S.P1 (1), R2.2
VCC_33: U$1.40 (AV+), U$6.3.3

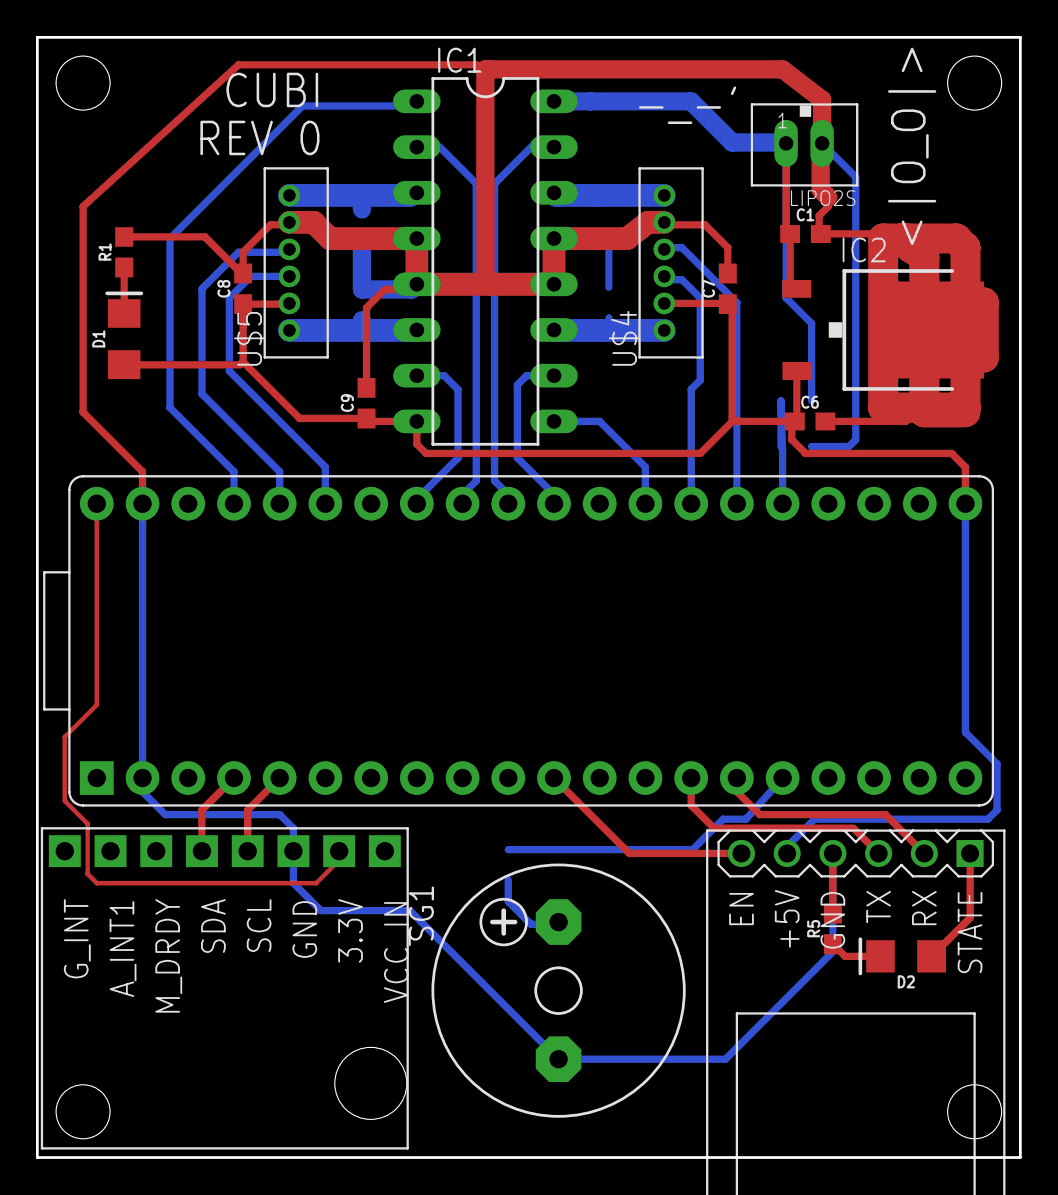
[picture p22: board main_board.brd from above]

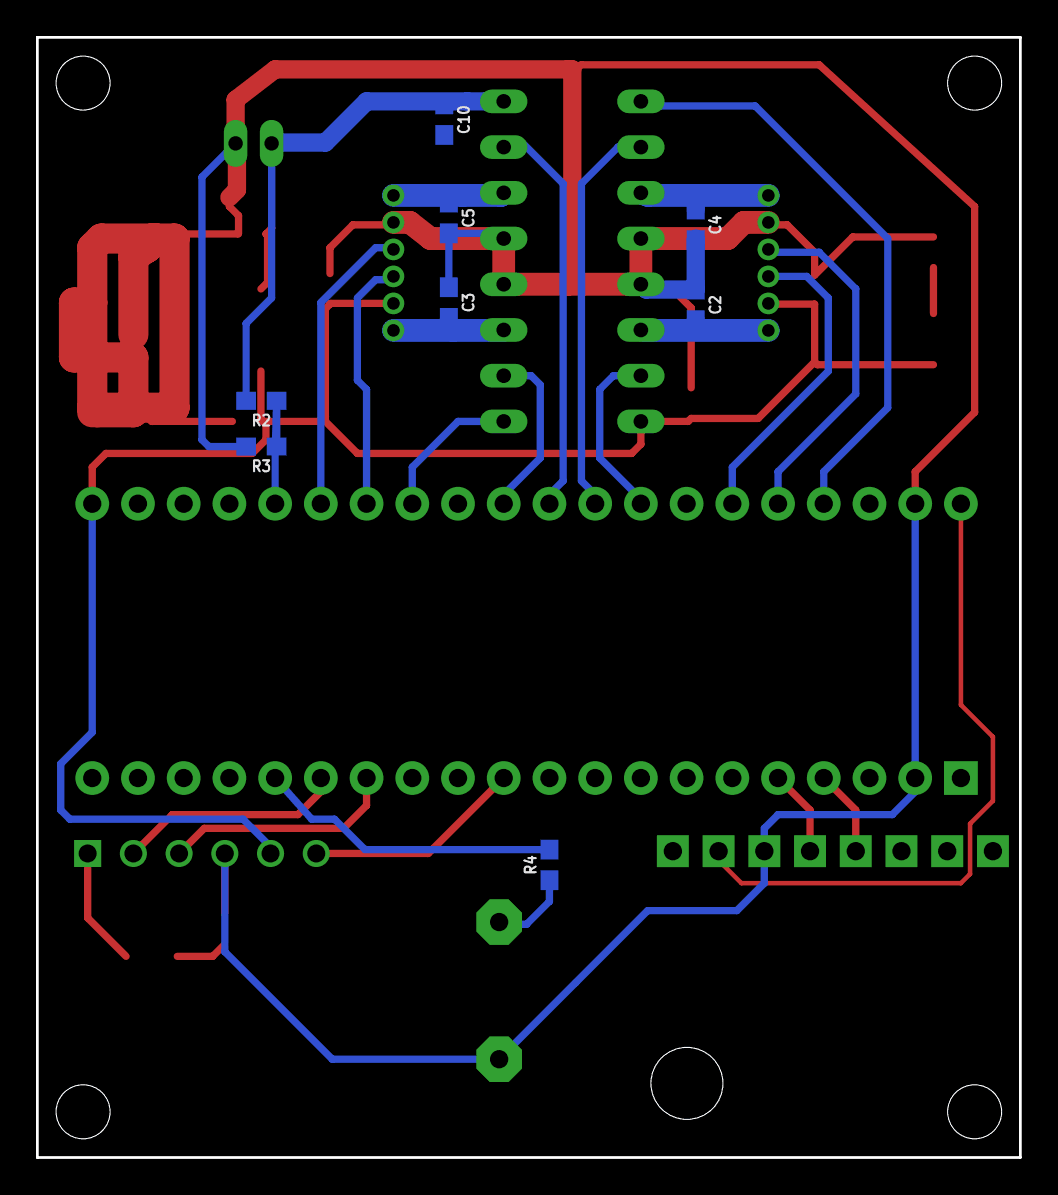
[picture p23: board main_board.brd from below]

Board: 2 copper layers, 54.6 x 62.2 mm, 26 parts (8 on the bottom side), 29 nets.

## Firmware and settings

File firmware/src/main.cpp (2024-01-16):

#include <stdlib.h>
#include <wirish/wirish.h>
#include <terminal.h>
#include <libmaple/adc.h>
#include <libmaple/timer.h>
#include <main.h>
#include "dc.h"
#include "buzzer.h"
#include "voltage.h"
#include "bt.h"
#include "model.h"
#include "imu.h"
#include "helpers.h"

#define NOSOUND 0
#define BAUDRATE 115200

// Without weights :
#define CART_KP 1000
#define CART_KI 10000
#define CART_KD 40

// With weights
// #define CART_KP 2000
// #define CART_KI 25000
// #define CART_KD 60
#define X_KP 0 //2
#define X_KI 0 //10

/*
  Timer2 controls the pwms 8, 9, 10 and 11
 */

int my_atoi(char *p, bool *success);
void default_cart_pole();
void p_demo_cart_pole();
void i_demo_cart_pole();
void d_demo_cart_pole();

bool isUSB = false;
bool isUSBForEver = true;
long counter = 0;
unsigned int hardwareCounter = 0;
bool readyToUpdateHardware = false;
bool led_state = false;

static float cart_kp = CART_KP;
static float cart_ki = CART_KI;
static float cart_kd = CART_KD;
static float cart_i_acc = 0;
static float cart_err = 0;
static float cart_last_err = 0;
static float cart_extra_rotation = 0;
static float adapted_cartgoal = 0;

static float cart_x_kp = X_KP;
static float cart_x_ki = X_KI;
static float cart_x_i_acc = 0;
static float cart_x_err = 0;

// Timming
static uint32 dt = 0;
static uint32 dt_ms = 0;
static uint32 dt_cart = 0;
static uint32 last_dt_cart = 0;
static uint32 time_micros = 0;
static uint32 old_time_micros = 0;
static uint32 time_ms = 0;
static uint32 old_time_ms = 0;
static uint32 half_max = (1 << 31);

TERMINAL_COMMAND(freq, "Returns the last measure of dt (the period of the main loop in micros)")
{
    terminal_io()->print(micros());
    terminal_io()->print(" = micros(), ");
    terminal_io()->print(millis());
    terminal_io()->print(" = millis(), dt = ");
    terminal_io()->print(dt);
    terminal_io()->print(" us, dt = ");
    terminal_io()->print(dt_ms);
    terminal_io()->print(" ms, freq = ");
    terminal_io()->print(1000000.0 / dt);
    terminal_io()->print(" Hz, dt_cart = ");
    terminal_io()->print(last_dt_cart);
    terminal_io()->print(" us, cart_freq = ");
    if (last_dt_cart != 0)
    {
        terminal_io()->print(1000000.0 / last_dt_cart);
        terminal_io()->println(" Hz");
    }
    else
    {
        terminal_io()->println(" I ain't no dividing by no zero");
    }
}

TERMINAL_COMMAND(carterr, "Debug function")
{
    terminal_io()->print("cart_err = ");
    terminal_io()->print(cart_err);
    terminal_io()->print(", cart_last_err = ");
    terminal_io()->println(cart_last_err);
}

TERMINAL_COMMAND(pwm, "[usage] pwm pwm_value1 pwm_value2")
{
    if (argc == 2)
    {
        bool success = false;
        int pwm1 = my_atoi(argv[0], &success);
        int pwm2 = my_atoi(argv[1], &success);
        _limit(&pwm1, MAX_PWM);
        _limit(&pwm2, MAX_PWM);
        dc_motor *motors = get_motors();
        motors[0].command = pwm1;
        motors[1].command = pwm2;
        terminal_io()->print("Setting pwms ");
        terminal_io()->print(pwm1);
        terminal_io()->print(" and ");
        terminal_io()->println(pwm2);
    }
    else
    {
        terminal_io()->println("[usage] pwm pwm_value1 pwm_value2");
    }
}

TERMINAL_COMMAND(rc, "Go to bluetooth serial mode")
{
    // Terminal management
    Serial1.begin(BAUDRATE);
    terminal_init(&Serial1);
    isUSB = false;
    isUSBForEver = false;
}
TERMINAL_COMMAND(usb, "Go to USB serial mode")
{
    // Terminal management
    isUSB = true;
    terminal_init(&SerialUSB);
    isUSBForEver = true;
}

TERMINAL_PARAMETER_BOOL(cartpole, "activates the cartpole mode", false);
TERMINAL_PARAMETER_FLOAT(cartgoal, "Angle goal for the inverted pendulum", 1.607);
TERMINAL_PARAMETER_FLOAT(criticangle, "Max angle we're allowed to aim around the vertical point to control the robot in rad", 0.005);

TERMINAL_COMMAND(cart, "goal(rads) [kp] [ki] [kd] [rotation]")
{
    if (argc >= 1)
    {
        cartpole = true;
        cartgoal = atof(argv[0]);
        // Resetting the accumulator
        cart_i_acc = 0;
    }
    if (argc >= 2)
    {
        cart_kp = atof(argv[1]);
        cart_ki = 0;
        cart_kd = 0;
    }
    if (argc >= 3)
    {
        cart_ki = atof(argv[2]);
        cart_kd = 0;
    }
    if (argc >= 4)
    {
        cart_kd = atof(argv[3]);
    }
    if (argc >= 5)
    {
        cart_extra_rotation = atof(argv[3]);
    }
}

TERMINAL_COMMAND(a, "debug")
{
    terminal_io()->println(adapted_cartgoal);
}

TERMINAL_COMMAND(c, "cartpole pid values: kp ki kd [rotation]")
{
    if (argc >= 3)
    {
        // Resetting the accumulator
        cart_i_acc = 0;
        cart_kp = atof(argv[0]);
        cart_ki = atof(argv[1]);
        cart_kd = atof(argv[2]);
    }
    if (argc >= 4)
    {
        cart_extra_rotation = atof(argv[3]);
    }
}

TERMINAL_COMMAND(d, "cartpole X pi values: kp ki")
{
    if (argc >= 2)
    {
        // Resetting the accumulator
        cart_x_i_acc = 0;
        cart_x_kp = atof(argv[0]);
        cart_x_ki = atof(argv[1]);
    }
}

TERMINAL_COMMAND(cd, "op command that sets the robot in inverted pendulum mode with default values")
{
    default_cart_pole();
}

TERMINAL_COMMAND(cdp, "Proportional control demo (needs an IMU)")
{
    p_demo_cart_pole();
}
TERMINAL_COMMAND(cdi, "Integral control demo (needs an IMU)")
{
    i_demo_cart_pole();
}
TERMINAL_COMMAND(cdd, "Derivate control demo (needs an IMU)")
{
    d_demo_cart_pole();
}
void default_cart_pole() {
    // Resetting the accumulator
    cart_i_acc = 0;
    cartpole = 1;
    model_reset();
    cart_kp = CART_KP;
    cart_ki = CART_KI;
    cart_kd = CART_KD;
    cart_x_kp = X_KP;
    cart_x_ki = X_KI;

    get_model()->mode = MODE_SPEED_CONTROL;
}

void p_demo_cart_pole() {
    // Resetting the accumulator
    cart_i_acc = 0;
    cartpole = 1;
    model_reset();
    cart_kp = CART_KP;
    cart_ki = 0;
    cart_kd = 0;
    cart_x_kp = 0;
    cart_x_ki = 0;

    get_model()->mode = MODE_SPEED_CONTROL;
}

void i_demo_cart_pole() {
    // Resetting the accumulator
    cart_i_acc = 0;
    cartpole = 1;
    model_reset();
    cart_kp = 0;
    cart_ki = CART_KI;
    cart_kd = 0;
    cart_x_kp = 0;
    cart_x_ki = 0;

    get_model()->mode = MODE_SPEED_CONTROL;
}

void d_demo_cart_pole() {
    // Resetting the accumulator
    cart_i_acc = 0;
    cartpole = 1;
    model_reset();
    cart_kp = 0;
    cart_ki = 0;
    cart_kd = CART_KD;
    cart_x_kp = 0;
    cart_x_ki = 0;

    get_model()->mode = MODE_SPEED_CONTROL;
}

void setup()
{
    // Wirish board specific init
    disableDebugPorts();

    pinMode(BOARD_LED_PIN, OUTPUT);
    pinMode(BOARD_BUTTON_PIN, INPUT);

    buzzer_init();
    if (!NOSOUND)
    {
        buzzer_play(MELODY_BOOT);
    }
    // Initializing IMU
    imu_init();

    model_init();
    motor_init();

    voltage_init();
    bt_init();

    // Terminal management
    Serial1.begin(BAUDRATE);
    // The HC05 is connected to Serial1
    terminal_init(&Serial1);
    ////terminal_init(&SerialUSB);

    digitalWrite(BOARD_LED_PIN, HIGH);

    digitalWrite(PWM12_ENABLE, HIGH);

    old_time_micros = micros();
    old_time_ms = millis();
    /*
    while(true) {
      delay(500);
      digitalWrite(BOARD_LED_PIN, LOW);
      delay(500);
      digitalWrite(BOARD_LED_PIN, HIGH);
    }*/
}

void loop()
{
    counter++;
    //delay(1);
    time_micros = micros();
    time_ms = millis();
    dt = time_micros - old_time_micros;
    dt_ms = time_ms - old_time_ms;

    if (dt > half_max)
    {
        // It probably means that the value reached its maximum and reseted
        uint32 max_value = 0;
        max_value = ~(max_value);
        dt = time_micros + (max_value - old_time_micros);
    }
    old_time_micros = time_micros;
    old_time_ms = time_ms;

    if (counter < 500)
    {
        digitalWrite(BOARD_LED_PIN, LOW);
    }
    else if (counter >= 500 && counter < 1000)
    {
        digitalWrite(BOARD_LED_PIN, HIGH);
    }
    else
    {
        counter = 0;
    }

    if (counter % 100 == 0)
    {
        // By default, the Serial used is the Bluetooth, except if a the SerialUSB is being written.
        // The isUSBForEver flag is used to persist in USB or in bluetooth, when asked through the terminal commands (rc/usb)
        if (SerialUSB.available() && !isUSB && isUSBForEver)
        {
            isUSB = true;
            terminal_init(&SerialUSB);
        }
    }

    if (digitalRead(BOARD_BUTTON_PIN))
    {
        default_cart_pole();
    }
    // Ticking IMU
    imu_tick();

    dt_cart = dt_cart + dt;

    if (cartpole && imu_is_checked)
    {
        imu_is_checked = false;
        cart_last_err = cart_err;
        // The angle goal is very slighlty modified with a PI controller so the X position of the robot (integrated through odometry) stays at what we want it to be
        cart_x_err = get_model()->x;
        cart_x_i_acc = cart_x_i_acc + cart_x_ki * cart_x_err * dt_cart / 1000000.0;
        _limit(&cart_x_i_acc, criticangle);
        float temp_sum = (cart_x_kp * cart_x_err + cart_x_i_acc);
        _limit(&temp_sum, criticangle);
        adapted_cartgoal = cartgoal + temp_sum;

        if (cart_x_kp == 0 && cart_x_ki == 0)
        {
            adapted_cartgoal = cartgoal;
        }
        cart_err = smooth_pitch - adapted_cartgoal;
        cart_i_acc = cart_i_acc + cart_ki * cart_err * dt_cart / 1000000.0;
        _limit(&cart_i_acc, MAX_PWM);
        // Putting minus signs was too exhausting.
        int speed = (int)(cart_kp * (cart_err) + cart_i_acc + cart_kd * (cart_err - cart_last_err) * 1000000 / dt_cart) * (-1);
        _limit(&speed, MAX_PWM);

        dc_motor *motors = get_motors();
        motors[0].speed_target = speed + cart_extra_rotation;
        motors[1].speed_target = speed - cart_extra_rotation;
        last_dt_cart = dt_cart;
        dt_cart = 0;
    }

    buzzer_tick();

    voltage_tick();
    terminal_tick();
    model_tick();
    dc_tick();

    return;
}

int my_atoi(char *p, bool *success)
{
    int k = 0;
    int sign = 1;
    if (*p == '-')
    {
        sign = -1;
        p++;
    }
    while (*p != '\0')
    {
        int value = *p - '0';
        if (value >= 0 && value <= 9)
        {
            k = k * 10 + value;
            p++;
        }
        else
        {
            *success = false;
            return 0;
        }
    }
    *success = true;
    return k * sign;
}

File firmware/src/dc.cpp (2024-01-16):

#include <stdio.h>
#include <terminal.h>
#include <wirish.h>
#include "dc.h"
#include "model.h"
#include "helpers.h"
#include "voltage.h"


// Dividers
static int divider = 0;
bool servoFlag = false;
static dc_motor motors[2];
HardwareTimer timer4(4);
HardwareTimer timer2(2);
int nbSpeeds = 0;
int nbDc = 0;
int prevNbDc = 0;

// PID parameters found with the Ziegler-Nichols method
TERMINAL_PARAMETER_INT(kp, "PID P", 20);
TERMINAL_PARAMETER_INT(ki, "PID I", 3); // Found 5, went lower because extreme changes in command would still create instabilities
TERMINAL_PARAMETER_INT(kd, "PID D", 2);
TERMINAL_PARAMETER_INT(enableodo, "enables/disables the odometry calculations", 1);


TERMINAL_COMMAND(nbspeeds, "Number of times the speed has been estimated since start (and the number of timer ovf)")
{
    terminal_io()->println(nbSpeeds);
    terminal_io()->println(nbDc);
}

// Result : 5us. Note that at 20KHz, we have 50us in between interrupts.
TERMINAL_COMMAND(eb, "Encoders benchmark")
{
    int avg = 0;
    for (int k=0; k<10000; k++) {
        int start = micros();
        encoders_update();
        int elapsed = micros()-start;
        avg += elapsed;
    }
    terminal_io()->println(avg/10000);
}

// Result (back when some of the calculation wasn't float): when speeds are not 0, ~340 us
// Result (full float) : when speeds are not 0, ~320 us...
TERMINAL_COMMAND(odobench, "Odometry benchmark")
{
    int avg = 0;
    for (int k=0; k<10000; k++) {
        int start = micros();
        increment_odometry();        
        int elapsed = micros()-start;
        avg += elapsed;
    }
    terminal_io()->println(avg/10000);
}
// Result (back when some of the calculation wasn't float) : when speeds are not 0, measure_ik ~90us, dx_dy ~90us.
// Result (full float) : when speeds are not 0, measure_ik ~73us, dx_dy ~108us.
TERMINAL_COMMAND(mikbench, "Measure IK benchmark")
{
    int avg = 0;
    int avg2 = 0;
    for (int k=0; k<10000; k++) {
        int start = micros();

        float linearSpeed;
        float rotationSpeed;
        measure_ik(&linearSpeed, &rotationSpeed);
        int elapsed = micros()-start;
        avg += elapsed;

        start = micros();
        // Constant speed over a duration -> distance
        float dt = SERVO_DT/1000.0;
        float dx = 0;
        float dy = 0;
        float dtheta = 0;
        
        dx_dy(linearSpeed, rotationSpeed, dt, &dx, &dy, &dtheta);       
        elapsed = micros()-start;
        avg2 += elapsed;
    }
    terminal_io()->print("measure_ik (us) : ");
    terminal_io()->println(avg/10000);
    terminal_io()->print("dx_dy (us) : ");    
    terminal_io()->println(avg2/10000);
}

TERMINAL_COMMAND(dct, "DC test")
{
    if (argc == 2) {
        int command1 = atoi(argv[0]);
        int command2 = atoi(argv[1]);
        _limit(&command1, MAX_PWM);
        _limit(&command2, MAX_PWM);
        
        motors[0].command = command1;
        motors[1].command = command2;

        terminal_io()->print("Sending to motor 1 : ");        
        terminal_io()->println(motors[0].command);
        terminal_io()->print("Sending to motor 2 : ");        
        terminal_io()->println(motors[1].command);
        
        dc_command();
    }
}


TERMINAL_COMMAND(em, "em")
{
    get_model()->mode = 0;
    motors[0].command = 0;
    motors[1].command = 0;
    dc_command();
    for (int k=0; k<2; k++) {
        motors[k].speed_target = 0;
    }
}

TERMINAL_COMMAND(enc, "Read encoders")
{
    while (!SerialUSB.available()) {
        for (int k=0; k<2; k++) {
            terminal_io()->print(motors[k].encoder_value);
            terminal_io()->print(" ");
        }
        terminal_io()->println();
        delay(10);
    }
}

TERMINAL_COMMAND(mode, "Sets how the motors are controlled (0 is speed control, 1 is PWM control, 2 is ikasserv)")
{
    if (argc == 1) {
        get_model()->mode = atoi(argv[0]);
    }
}

TERMINAL_COMMAND(er, "Encoders reset")
{
    for (int k=0; k<2; k++) {
        motors[k].encoder_value = 0;
        motors[k].nb_errors = 0;
    }
}

TERMINAL_COMMAND(es, "Encoders speed")
{
    //while (!SerialUSB.available()) {
        for (int k=0; k<2; k++) {
            terminal_io()->print(motors[k].speed);
            terminal_io()->print(" ");
        }
        terminal_io()->println(" [imp/SPEED_DT]");

        for (int k=0; k<2; k++) {
            terminal_io()->print(firmware2SI(motors[k].speed)*RAD2DEG);
            terminal_io()->print(" ");
        }
        terminal_io()->println(" [deg/s]");
        //delay(10);
    //}
}

TERMINAL_COMMAND(nberrors, "Number of errors read")
{
    while (!SerialUSB.available()) {
        for (int k=0; k<2; k++) {
            terminal_io()->print(motors[k].nb_errors);
            terminal_io()->print(" ");
        }
        terminal_io()->println();
        delay(10);
    }
}

TERMINAL_COMMAND(st, "Speed target")
{
    if (argc == 2) {
        motors[0].speed_target = atoi(argv[0]);
        motors[1].speed_target = atoi(argv[1]);
    }
}

TERMINAL_COMMAND(stdeg, "Speed target in deg/s")
{
    if (argc == 2) {
        motors[0].speed_target = SI2firmware(DEG2RAD*atoi(argv[0]));
        motors[1].speed_target = SI2firmware(DEG2RAD*atoi(argv[1]));
    }
}

TERMINAL_COMMAND(printmotor, "Prints the current motor info")
{
    for (int k=0; k<2; k++) {
        terminal_io()->print("Motor ");
        terminal_io()->println(k);
        
        terminal_io()->print("rb_pos ");
        terminal_io()->println(motors[k].rb_pos);
        
        terminal_io()->print("encoder_value ");
        terminal_io()->println(motors[k].encoder_value);

        terminal_io()->print("encoder_phase ");
        terminal_io()->println(motors[k].encoder_phase);

        terminal_io()->print("dir ");
        terminal_io()->println(motors[k].dir);

        terminal_io()->print("speed ");
        
        terminal_io()->println(motors[k].speed);

        terminal_io()->print("prev_speed ");
        terminal_io()->println(motors[k].prev_speed);

        terminal_io()->print("speed_target ");
        terminal_io()->println(motors[k].speed_target);

        terminal_io()->print("acc ");
        terminal_io()->println(motors[k].acc);

        terminal_io()->print("command ");
        terminal_io()->println(motors[k].command);
        terminal_io()->println();

        terminal_io()->print("divider ");
        terminal_io()->println(divider);

        terminal_io()->println("enc_positions ");
        for (int i = 0; i < SPEED_RB; i ++) {
            terminal_io()->println(motors[k].encoder_rb[(motors[k].rb_pos + i)%SPEED_RB]); 
        }
        terminal_io()->println();   
    }
}

dc_motor * get_motors() {
    return motors;
}
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

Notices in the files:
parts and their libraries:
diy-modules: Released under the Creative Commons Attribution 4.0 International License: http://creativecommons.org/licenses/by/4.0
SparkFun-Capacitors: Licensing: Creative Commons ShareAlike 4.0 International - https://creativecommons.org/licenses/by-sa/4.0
